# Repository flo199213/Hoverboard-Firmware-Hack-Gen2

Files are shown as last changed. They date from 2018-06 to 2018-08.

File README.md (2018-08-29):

#### Updates:
````
- Firmware is ready.
- Sadly I can not support any issues. I'm not a student, less free time :)
````

### Hoverboard-Firmware-Hack-Gen2

Hoverboard Hack Firmware Generation 2 for the Hoverboard with the two Mainboards instead of the Sensorboards (See Pictures).

This repo contains open source firmware for generic Hoverboards with two mainboards. It allows you to control the hardware of the new version of hoverboards (like the Mainboard, Motors and Battery) with an arduino or some other steering device for projects like driving armchairs.

The structure of the firmware is based on the firmware hack of Niklas Fauth (https://github.com/NiklasFauth/hoverboard-firmware-hack/). Because of a different model of processor (GD32F130C8 instead of STM32F103) it was not possible to use the same firmware and it has to be written from scratch (Different hardware, different, pins, different registers :( )

- This project requires knowledge of the initial project linked above.
- At the current point I am not able to support any questions or issues - sorry!

---

#### Hardware
otter

The hardware has two main boards, which are different equipped. They are connected via USART. Additionally there are some LED PCB connected at X1 and X2 which signalize the battery state and the error state. There is an programming connector for ST-Link/V2 and they break out GND, USART/I2C, 5V on a second pinhead.

The reverse-engineered schematics of the mainboards can be found here:
https://github.com/flo199213/Hoverboard-Firmware-Hack-Gen2/blob/master/Schematics/HoverBoard_CoolAndFun.pdf

---

#### Flashing
The firmware is built with Keil (free up to 32KByte). To build the firmware, open the Keil project file which is includes in repository. Right to the STM32, there is a debugging header with GND, 3V3, SWDIO and SWCLK. Connect GND, SWDIO and SWCLK to your SWD programmer, like the ST-Link found on many STM devboards.

- If you never flashed your mainboard before, the controller is locked. To unlock the flash, use STM32 ST-LINK Utility or openOCD.
- To flash the STM32, use the STM32 ST-LINK Utility as well, ST-Flash utility or Keil by itself.
- Hold the powerbutton while flashing the firmware, as the controller releases the power latch and switches itself off during flashing

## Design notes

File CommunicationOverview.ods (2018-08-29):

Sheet: Frames
Direction | Byte Count | 0 | 1 | 2 | 3 | 4 | 5 | 6 | 7 | 8 | 9 | 10
Master → Steering | 2 | / | \n
 |  | char | char
Steering → Master | 8 | / | Speed |  | Steer |  | CRC |  | \n
 |  | char | int16 |  | int16 |  | uint16 |  | char
Master → Slave | 10 | / | PWM |  | Identifier | Value | value | Bits | CRC |  | \n
 |  | char | int16 |  | uint8 | int16 |  | uint8 | uint16 |  | char
Slave → Master | 5 | / | Bits | CRC |  | \n
 |  | char | uint8 | uint16 |  | char
Slave → Bluetooth | 11 | / | Identifier |  | 0 | ± | Value |  |  |  |  | \n
 |  | char | char1 | char2 | uint8 | char | char1 | char2 | char3 | char4 | char5 | char
Bluetooth → Slave | 11 | / | Identifier |  | Read/Write | ± | Value |  |  |  |  | \n
 |  | char | char1 | char2 | uint8 | char | char1 | char2 | char3 | char4 | char5 | char

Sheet: Identifierlist
Slave ↔ Bluetooth
Identifier | Meaning | Location | Range
0 | Battery Master | Master | Value*100
1 | Current DC Master | Master | Value*100
2 | Current DC Slave | Slave | Value*100
3 | Real Speed Master | Master | Value*100
4 | Real Speed Slave | Slave | Value*100
5 | Beeps backwards | Master | Off=0, On=1
6 | Music Box (Master lower) | Master | Off=0, On=1
7 | Horn (Master upper) | Master | Off=0, On=1
8 | LED Hue | Slave | 0-764
9 | LED Saturation | Slave | 0-128
10 | LED Brightness | Slave | 0-63
11 | LED Mode | Slave | LED_OFF = 0, LED_HSB = 1, LED_HSB_BLINK = 2, LED_HSB_FADE = 3, LED_HSB_STROBE = 4
12 | LED Fading Speed | Slave | 200-1000
13 | LED Blink Speed | Slave | 700-2400
14 | LED Strobe Speed | Slave | 0-1000

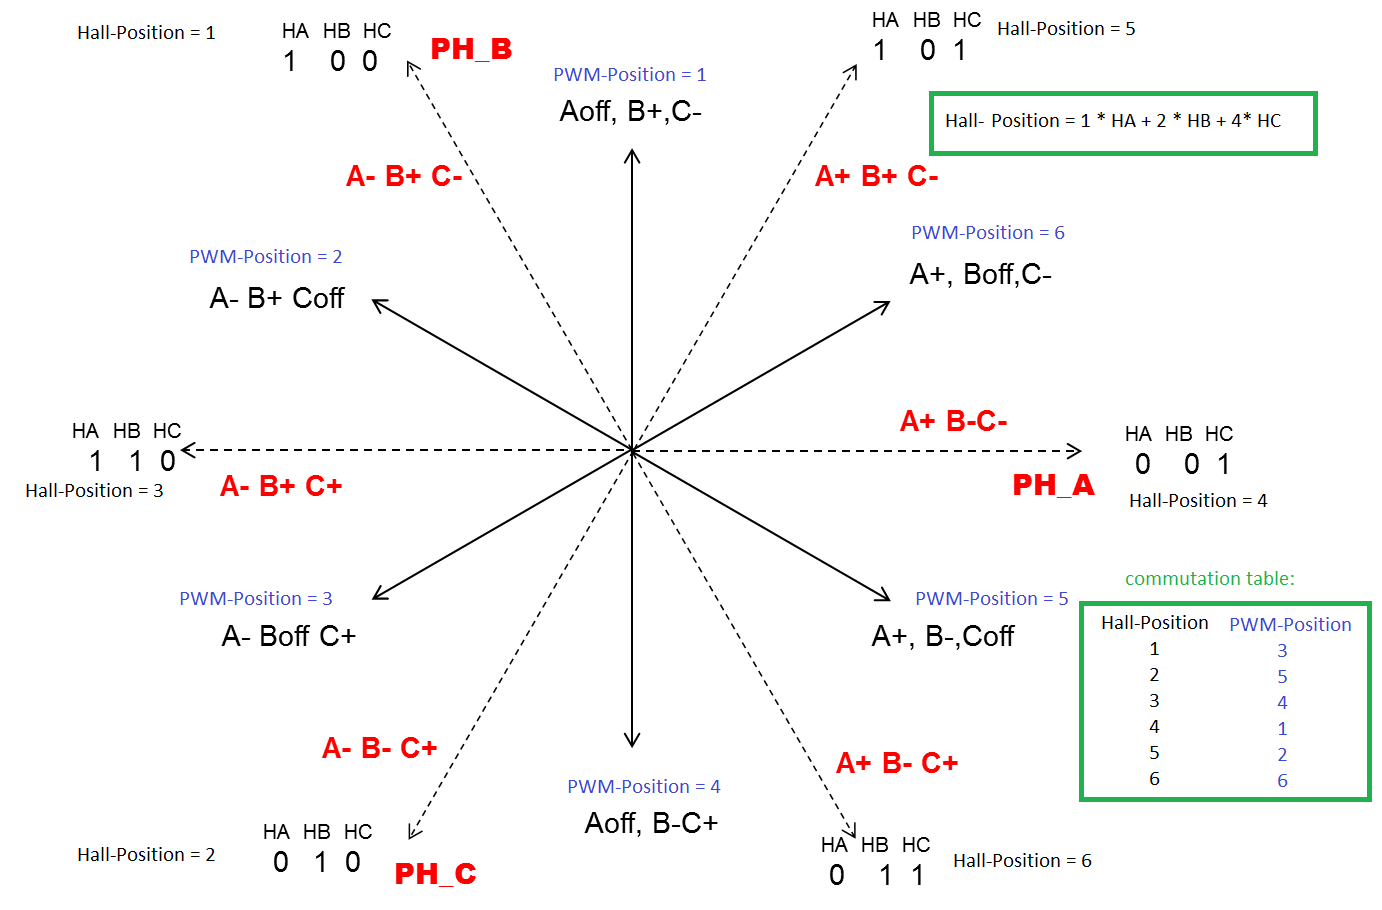
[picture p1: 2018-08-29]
Raumzeigerdiagramm.png

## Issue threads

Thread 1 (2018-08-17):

Updates

drbytes, 2018-08-17:
I've managed to flash the two boards from a eslide 650 with this.
Had to unlock the firmware first on both boards and solder a header. My boards have a different layout. This is the first time working with STLINK/STM32, 0 prior experience but flashing with the keil sdk went well, just keep holding the power button or it doesn't work. Good job on this firmware, I'll see if I can get it to interface with a pi this weekend.
Is the work on this ongoing?

gaucho1978, 2019-04-13:
I'll try the same. Is it a way to restore the hoverboard after playing with this hack?

Closed 2018-08-17.

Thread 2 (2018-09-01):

#include "arm_math.h"

drbytes, 2018-09-01:
Hi, I installed all the relevant software packs in Keil uVision ... at least that what I thought but I get a compilation error in main.c around line
`47: #include "arm_math.h" `
resulting in
```
Src\main.c(47): error:  #5: cannot open source input file "arm_math.h": No such file or directory
  #include "arm_math.h"
```

Do you know what I'm missing? (keil n00b)

drbytes, 2018-09-01:
I've commented the line and it builds.

Johnvan, 2019-02-24:
I have a similar problem with an adafruit MP3 program that uses arm_math.h, what do I have to do to fix this thing.
ERROR: arm_math.h: No such file or directory

pieterjanbuntinx, 2019-02-26:
It now works for me. To solve the other error I got I had to enable this:
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

Johnvan, 2019-02-28:
I have no idea what you are trying to tell me about **Enabling this,** what and how. Where is this Options for Target.

gaucho1978, 2019-04-19:
> You have to include the path C:\Keil_v5\ARM\PACK\ARM\CMSIS\5.4.0\CMSIS\Include in the "Options for Target..."  > C/C++. Afterwards it compiles al the c-files but it gets stuck on the other issue that's reported in this repo.

in my case the correct folder is: C:\Users\GauchoHP\AppData\Local\Arm\Packs\ARM\CMSIS\5.5.1\CMSIS\Include

after doing this it correctly compile.

renmalek7, 2020-04-08:
Hi. Were you able to flash this firmware?

Johnvan, 2020-04-09:
I updated my IDE and the fault went away. Thankyou for your assistance however, much appreciated.

weiminshen99, 2023-05-19:
The <arm_math.h> and other related .h files may also be found at this repository:
https://github.com/PaulStoffregen/arm_math

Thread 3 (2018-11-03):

Hoverboard.axf not found

bugiworks, 2018-11-03:
I appreciate your work, after 1 board hoverboard, i want to try this one also.

when i try to build with keil, i get the error
.\Objects\Hoverboard.axf: error: L6031U: Could not open scatter description file .\Objects\Hoverboard.sct: No such file or directory
Not enough information to list image symbols.
Not enough information to list load addresses in the image map.
Finished: 2 information, 0 warning, 0 error and 1 fatal error messages.
".\Objects\Hoverboard.axf" - 1 Error(s), 0 Warning(s).
Target not created.

any solution? or any direct hex files do you have?
By the way, the board im using has GD32F103 not F130, i have downloaded the pack for 103 but im not sure if it works same.

pieterjanbuntinx, 2018-12-21:
Hi @kevin0932,
No, I did not. But I found [a fork](https://github.com/btsimonh/Hoverboard-Firmware-Hack-Gen2) of this repo that compiles. I have not managed to get it uploaded to my hoverboard controller, I don't have a STLink but I'm using a STM32 Discovery board, so that's probably the problem.

bugiworks, 2018-12-25:
Unfortunately i couldnt find any solution.

pieterjanbuntinx, 2019-02-26:
It now works for me. To solve this error I had to enable this:
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

renmalek7, 2020-04-08:
Hi. Were you able to flash this firmware?

pieterjanbuntinx, 2020-04-08:
Yes, I was able to flash it. It works great. What are you stuck on?

renmalek7, 2020-04-08:
I have a different board, it's also a GD32F130. Before flashing the firmware, How can I tell if the Pins are the same?
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

pieterjanbuntinx, 2020-04-08:
You could perhaps measure continuity using a multimeter from the pins of the MCU to the peripherals. If that corresponds to the pinout in the code it should work. That will be quite some work though, so if you think that the layout of the PCB looks about the same as the one of this repo, you could perhaps just try it out (at your own risk). Replacement boards are not that expensive from AliExpress

renmalek7, 2020-04-08:
ok, I will do that and post the results. Do you know if there is a way to pull the original firmware from the board? Would it be posible to write it back in the board if I fail and its not burned l?

pieterjanbuntinx, 2020-04-08:
No I don't think so. I thought it was locked or something. It has something to do with the options bytes

renmalek7, 2020-04-08:
ok, thank you very much for you time : )

Harsh2210, 2020-06-16:
> I have a different board, it's also a GD32F130. Before flashing the firmware, How can I tell if the Pins are the same?
> 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

Were you able to flash the firmware? I am using the same motherboard. I wanted to know whether the pinouts are same for this one.

yodaco, 2022-07-23:
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

Did it work?!?

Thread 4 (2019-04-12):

Use Pwm or ppm input, avoiding the need of arduino

gaucho1978, 2019-04-12:
Can I modify your code to control hoverboard via ppm or 3 pwm instead of a uart?
Can I use the following inputs to receive pwm or ppm?:
-pa7(L1)
-pa11(L2)
-pc15(switch k1)

Can I use external switch instead of K1 switch in order to assign to it another funcion?

Can I use pc13(x3.1 output) or pa1(x2.1 output) to generate a pwm signal?

gaucho1978, 2019-05-12:
done here: https://github.com/gaucho1978/CHEAP-LAWNMOWER-ROBOT-FROM-HOVERBOARD/blob/master/README.md

Closed 2019-05-12.

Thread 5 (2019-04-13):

Restore hoverboard

gaucho1978, 2019-04-13:
Is it there a way to restore the hoverboard after playing with this hack?

teixeluis, 2019-06-21:
That is a pertinent question. Anyone have been successful at dumping the original firmware via ST-Link? Is it locked in most of not every board?

If a dump of the firmware + eeprom + config bits is feasible, eventually the device could be restored (I would put very little hope that the device flash is not protected though..).

Cheers,

Luis Teixeira

renmalek7, 2020-04-06:
Anyone did it?

renmalek7, 2020-04-08:
Hi. Were you able to flash this firmware?

weiminshen99, 2023-05-19:
I have saved the original flash for both Master and Slave board, if anyone is still interested.

teixeluis, 2023-05-19:
@weiminshen99  cool. Yes I would have interest in taking a peek. Cheers

weiminshen99, 2023-05-19:
The saved .bin files are at https://github.com/weiminshen99/GD32-hover-master-slave.git, under the directory Factory_Flash.

I have saved them after I unlocked boards, but I never test them because my boards are all occupied for other purposes. Good luck, and let me know if they work or not. Thanks!

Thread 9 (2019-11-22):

Mention "TT-SD2.2" in docs

gnbl, 2019-11-22:
It should be mentioned that this project is based on a PCB with silkscreen markings "TT-SD2.2", which seems to be a TaoTao hoverboard controller.
I have two of these, one 6.5" Cool&Fun and an 8" "M110".
The former has water damage on the primary control board and fries the high-side switch of phase A. It seems I'll have to dig through the conformal coating to measure whether the drivers or the sensing or even the MCU is defective...

renmalek7, 2020-04-08:
Hi. Were you able to dig through the coating? Were you able to flash the firmware?

gnbl, 2020-04-24:
I have not yet attempted reflashing nor repair.

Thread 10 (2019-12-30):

Please add a makefile for my online compiler :-)

RoboDurden, 2019-12-30:
Hello from Germany :-)
I would like to add your repo to my online compiler www.pionierland.de/hoverhack
videos: https://www.youtube.com/playlist?list=PLa9VLvJBLbTMmpslED2FMClIBv5URBMIa

But you only offer the Keil project files. If you are already compiling with GCC, a port should be possible: https://community.arm.com/developer/tools-software/oss-platforms/f/gnu-toolchain-forum/45142/how-to-move-from-keil-to-linux

Ideas welcome !
www.robo4future.de :-)

RoboDurden, 2020-01-14:
no answer :'(

renmalek7, 2020-04-06:
Hello. Were you able to move the repo to your online compiler? I am working with this firmware and I would appreciate your advice. Could you please mail me to renmalek7@gmail.com

Thank you very much : )

RoboDurden, 2020-04-06:
No, i am not experienced enough to copy and paste a Makefile :-/
A pity because adding repos to my online compiler just takes one line of code. Today i added all three repos of  https://github.com/EmanuelFeru

renmalek7, 2020-04-06:
What about Florian's firmware (this branch)? Were you able to flash it in a Gen2 board?

RoboDurden, 2020-04-06:
I have no Gen2 board where there is a control board for either side.

renmalek7, 2020-04-06:
Do you have 20 min for a video call? I am having trouble with the firmware and maybe you can advise me. Do you have skype?

renmalek7, 2020-04-08:
please, I just need someone to tell me how to indentify the pin conection in the board : (

RoboDurden, 2020-04-08:
You are spoliing my issue here to kindly ask for a makefile.

renmalek7, 2020-04-08:
I am really sorry. Thats why I left my email. Could you plase help me?

bricobi5, 2022-06-05:
Hi I have 4 gen2 motherboard that I can't flash so I try Florian's firmware
but where can i find it?

RoboDurden, 2022-06-05:
https://github.com/flo199213/Hoverboard-Firmware-Hack-Gen2/tree/master/HoverBoardGigaDevice
But as it still has no makefile, i can not include it to my online compiler :-(
I guess you have to install Keil to open the .uvoptx µVision 5 project files :-((
Someone who does not dislike Linux so strongly as i do might easily generate that makefile for me/us :-/

BastelPichi, 2022-07-23:
> https://github.com/flo199213/Hoverboard-Firmware-Hack-Gen2/tree/master/HoverBoardGigaDevice But as it still have no makefile, i can not include it to my online compiler :-( I guess you have to install Keil to open the .uvoptx µVision 5 project files :-(( Someone who does not dislike Linux so strongly as i do might easily generate that makefile for me/us :-/

Incoperating #16 may fix the issue. Compiling with PIO should be possible, but i dont know what amount of recoding this would take.

RoboDurden, 2022-07-23:
For a Linux believer a make file should be no issue at all. But I am rather a Linux hater.
Yet if you tell me how to install PlatformIO on my Ubuntu vserer and which exact command line will successfully compile the firmware, I would add platform Io support to my online compiler :-)

BastelPichi, 2022-07-24:
Well to install PIO, you get quite good docs here: [https://docs.platformio.org/en/latest/core/installation/methods/index.html](https://docs.platformio.org/en/latest/core/installation/methods/index.html)

To compile the project, all you need to do is run `pio run` in the `HoverBoardGigaDevice`directory.
The build is saved at `HoverBoardGigaDevice/.pio/build/GD32F130C8T6/` theres a firmware.bin and a firmware.elf, I assume they are both the same, but I would try to firmware.elf first.

The first build takes quite some time as it downloads alot, however then builds run within a few seconds.

PS: Lol ich könnte auch einfach Deutsch schreiben
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

BastelPichi, 2022-09-03:
Any update on this?

RoboDurden, 2022-09-03:
no time (time = happiness) to add the PIO support. sorry.

BastelPichi, 2022-09-04:
Ok, I broke my STLink anyways for now xD

weiminshen99, 2023-04-24:
Here is a repository for Makefile, if you are still interested:
https://github.com/weiminshen99/GD32-hover-master-slave

RoboDurden, 2023-04-24:
Yes great,  i still would like to add a gen2 firmware to my online compiler.
Your folder structure

https://github.com/weiminshen99/GD32-hover-master-slave/tree/main/Drivers/GD32F1x0_standard_peripheral/Source

 is a bit different then my gen 2.x firmware

https://github.com/RoboDurden/Hoverboard-Firmware-Hack-Gen2.x/tree/main/HoverBoardGigaDevice/RTE/Device/GD32F130C6

But I guess I can port your makefile.

If your makefile generates a working gen2.0 binary i would add your report to my online compiler. It might take a year before I proceed with the makefile for my repo...

RoboDurden, 2023-04-24:
no but i have made quite a lot of reverse engeniering: https://github.com/RoboDurden/Hoverboard-Firmware-Hack-Gen2.x/tree/main/Schematics_2.0

RoboDurden, 2023-04-26:
So i have added your repo to my online compiler. But i forked it because i needed to switch to a gcc inline compiler directive. Still get a warning

```
Src/bldc.c:90:38: warning: always_inline function might not be inlinable [-Wattributes]
   90 | __attribute__((always_inline))  void blockPWM(int pwm, int pwmPos, int *y, int *b, int *g) //org __INLINE not known in gcc

```
but the code compiles:  https://pionierland.de/hoverhack/?p=gen2
Maybe someon can test it.

I also needed to increase a char buffer from 5 to 7 in comsBluetooth.c to remove sprintf warnings:

```
void SendBluetoothDevice(uint8_t identifier, int16_t value)
{
	int index = 0;
	char charVal[7];

```

This should also apply to your compiler ?

Thanks again.

weiminshen99, 2023-04-26:
Thanks for adding my repo!

I have made the two changes you suggested and compiled here successfully and pushed the changes into my repo.

If you like, you could try to compile again to see if you can get rid of the warming (replace “_INLINE” by “inline”).

Have a good day!

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

RoboDurden, 2023-04-27:
Yes i would like to add your original and not my fork so you might be motivated to get involved.
But I had already tried the official c inline and it does.not compile:

/usr/lib/gcc/arm-none-eabi/9.2.1/../../../arm-none-eabi/bin/ld: build/bldc.o: in function `CalculateBLDC':
/var/www/html/pionierland/public/hoverhack/source/robodurden_gd32-hover-master-slave/Src/bldc.c:214: undefined reference to `blockPWM'
collect2: error: ld returned 1 exit status
make: *** [Makefile:185: build/firmware.elf] Error 1

I can remove the inline altogether and i compiles without warning. Is that function really that time critical that there is no time to make a function call ?

RoboDurden, 2023-04-27:
I See that the blockPWM function is used only once anyway : https://github.com/weiminshen99/GD32-hover-master-slave/blob/main/Src/bldc.c#L214

So simply copy the code there ?

I think it should be possible to make the function code a #define , that might be another was to get rid of that inline word ?

weiminshen99, 2023-04-27:
I have taken out the “__INLINE”, and please compile again. Thanks!

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

RoboDurden, 2023-04-27:
Fine, i switched the repo back to yours :-)

https://pionierland.de/hoverhack/?p=gen2

Would be nice if you could add a simple arduino example that spins the two motors a bit forward and backwards.
This seems to be too much: https://github.com/gaucho1978/CHEAP-LAWNMOWER-ROBOT-FROM-HOVERBOARD/tree/master/ArduinoFirmware

For my Gen 2.x firmware i rewrote all the serial communication, so people can not rely on my arduino example when using your firmware.
The original https://github.com/flo199213/Hoverboard-Firmware-Hack-Gen2/tree/master/PPMDeviceArduino_V1.0/PPMDevice is also overloaded with PPM rc-control :-/

Ideas welcome :-)

weiminshen99, 2023-04-28:
Please open an issue at the repos: https://github.com/weiminshen99/GD32-hover-master-slave
and I will add something as you requested there. Thanks!

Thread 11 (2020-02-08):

GD32F103 board?

abrarakram19, 2020-02-08:
Can this firmware be flashed on two red coloured boards with GD32F103 MCU? Please let me know if it is possible or any link for this type.

renmalek7, 2020-04-08:
Hi. Were you able to flash this firmware in those red boards? Do you still need help?

baranchuk, 2020-04-10:
I try to flash it on red boards. It not work for me

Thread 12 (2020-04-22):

Error flashing with ST-LINK utility

JMarceloCasanova, 2020-04-22:
Hello! I'm having an error flashing the firmware with ST-LINK.

So what I have done is: compiled the firmware with Keil to have the binaries, connected the st-link v2 with the board and unlocked the flash by resetting the option bytes, cleared the memory and then I get this error:
: Unexpected error
: Error occured during program operation!
: Programming error @ 0x08000000!
I'v tried pressing the button and changing some speeds but with no success.

My board's model is TT-SD2.2 with a gd32f130c8t6

andresiko, 2020-07-22:
Any progresa @JMarceloCasanova ?

drphil3d, 2022-02-02:
having the same issue

rokars, 2022-06-06:
i used the keil flash -> download to program directly from keil, works

AlfreddGco, 2023-12-01:
Try with `st-flash --reset write ./firmware.bin 0x08000000`

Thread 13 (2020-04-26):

Split Board "Jiaan" with GD32F130C6

t-oster, 2020-04-26:
Hi,

I have a Hoverboard with two almost identical boards labeled "Jiaan". I am trying to get this to work, however I am not experienced with ARMs so far (only AVRs) and not so used to reverse engineering.
I already found out it uses a GD32F130C6 instead of GD32F130C8 (32kb instead of 64kb flash etc).
I unlocked both controllers and I can flash files, which can successfully be read after that, so I think flashing is fine.
I guess the basics are similar to the boards this firmware is written for, but there must be differences (e.g. other PINs used?). I'd like to provide a patch for this firmware to also work with those boards, but I'm stuck.

I am trying to get some answer from the board, I tried to send something on both USARTs or blink some Pin I think is connected to an LED but nothing so far.

Has anybody already seen this board an can help me out?

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

t-oster, 2020-04-29:
At least the Master/Slave UART seems to be on the correct PINs. I can communicate with the controller now. Any Idea how I can find out the pin-assignments without destructing the board? It's not easy for me to follow the tracks on the board, but I guess I should not just set all pins as output and set/reset them in order to look for which LED is blinking or if the motor does something, because if there is an output from another IC connected I might short circuit it...

t-oster, 2020-04-30:
OK, now I know the Pins for the Light-Barriers, the Buzzer, the hall sensor, power button and power-latch.
Now I only need to find the pins for the 6 channels for the motor. Any idea how I can easily trace them? I guess if I accidentally switch the same channel high and low at the same time I would get a short circuit? Are the outputs usually pulled up or down externally?

t-oster, 2020-05-02:
Nevermind, I got it to work basically. The motors are on the same pin as on your board. The biggest problem with mine is that the second UART is not broken out, so I have to use the TX for the slave and the RX for the arduino....
maybe I will send a PR after cleaning a bit. However here are my PINs so far:
```c
#ifndef DEFINES_H
#define DEFINES_H

#include "gd32f1x0.h"
#include "../Inc/config.h"

// LED defines

#define UPPER_LED_PIN GPIO_PIN_5
#define UPPER_LED_PORT GPIOB
#define LOWER_LED_PIN GPIO_PIN_8
#define LOWER_LED_PORT GPIOB

// Brushless Control DC (BLDC) defines
// Channel G
#define RCU_TIMER_BLDC RCU_TIMER0
#define TIMER_BLDC TIMER0
#define TIMER_BLDC_CHANNEL_G TIMER_CH_2
#define TIMER_BLDC_GH_PIN GPIO_PIN_10
#define TIMER_BLDC_GH_PORT GPIOA
#define TIMER_BLDC_GL_PIN GPIO_PIN_15
#define TIMER_BLDC_GL_PORT GPIOB
// Channel B
#define TIMER_BLDC_CHANNEL_B TIMER_CH_1
#define TIMER_BLDC_BH_PIN GPIO_PIN_9
#define TIMER_BLDC_BH_PORT GPIOA
#define TIMER_BLDC_BL_PIN GPIO_PIN_14
#define TIMER_BLDC_BL_PORT GPIOB
// Channel Y
#define TIMER_BLDC_CHANNEL_Y TIMER_CH_0
#define TIMER_BLDC_YH_PIN GPIO_PIN_8
#define TIMER_BLDC_YH_PORT GPIOA
#define TIMER_BLDC_YL_PIN GPIO_PIN_13
#define TIMER_BLDC_YL_PORT GPIOB

// Timer BLDC short circuit emergency shutoff define
#define TIMER_BLDC_EMERGENCY_SHUTDOWN_PIN GPIO_PIN_12
#define TIMER_BLDC_EMERGENCY_SHUTDOWN_PORT GPIOB

// Hall sensor defines
#define HALL_A_PIN GPIO_PIN_0
#define HALL_A_PORT GPIOA
#define HALL_C_PIN GPIO_PIN_11
#define HALL_C_PORT GPIOB
#define HALL_B_PIN GPIO_PIN_1
#define HALL_B_PORT GPIOA

// Usart master slave defines
#define USART_MASTERSLAVE USART1
#define USART_MASTERSLAVE_TX_PIN GPIO_PIN_2
#define USART_MASTERSLAVE_TX_PORT GPIOA
#define USART_MASTERSLAVE_RX_PIN GPIO_PIN_3
#define USART_MASTERSLAVE_RX_PORT GPIOA

// ADC defines
#define VBATT_PIN	GPIO_PIN_4
#define VBATT_PORT GPIOA
#define VBATT_CHANNEL ADC_CHANNEL_4
#define CURRENT_DC_PIN	GPIO_PIN_6
#define CURRENT_DC_PORT GPIOA
#define CURRENT_DC_CHANNEL ADC_CHANNEL_6

// Self hold defines
#define SELF_HOLD_PIN GPIO_PIN_2
#define SELF_HOLD_PORT GPIOB

// Button defines
#define BUTTON_PIN GPIO_PIN_5
#define BUTTON_PORT GPIOA

// Buzzer defins
#define BUZZER_PIN GPIO_PIN_9
#define BUZZER_PORT GPIOB

// Charge state defines
#define CHARGE_STATE_PIN GPIO_PIN_15
#define CHARGE_STATE_PORT GPIOC

Closed 2020-05-02.

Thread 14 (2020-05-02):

ADC control with two potentiometers

vischio96, 2020-05-02:
Hi all,

these two identical mainboards are pretty common in hoverboards, and i have a lot of them at home. Does anyone know if there's a way to control the two boards with 2 differents ADC inputs (ex two potentiometers) as the mainboard that NiklasFauth uses?

From the reverse engineered schematics i see that the two lightbarriers sensors uses two ADC pins (PA7 and PA11) and they seems unused in the code, but i'm not that good at programming.
The only way i know to control these mainboards is using PPM with an Arduino board.

Could anyone help me? Thank you a lot.

andresiko, 2020-07-22:
Have you succeeded flashing these boards? I have an tt-sd 2.2 with gd32f130c8t6, and I don't know if this firmware will work on it.

zulkep, 2021-06-16:
have you got to connect the potentiometers directly to the board?

Jebumon, 2022-04-25:
Hi all,

I have hoverboard control board, using GD32F130C8T6. Anyone know how to re-program his MCU ?
could anyone help me ?

alexei0kazachina, 2023-06-02:
Да пишите мне, я смогу помоч.

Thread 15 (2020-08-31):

No compiling , error in adc

centiane, 2020-08-31:
No compiling ok, this error show, help me, please.

*** Using Compiler 'V5.06 update 6 (build 750)', folder: 'C:\Keil_v5\ARM\ARMCC\Bin'
Rebuild target 'Target 1'
compiling setup.c...
Src\setup.c(343): error:  #167: argument of type "dma_parameter_struct" is incompatible with parameter of type "dma_parameter_struct *"
  	dma_init(DMA_CH0, dma_init_struct_adc);
Src\setup.c(365): error:  #20: identifier "ADC_EXTTRIG_REGULAR_SWRCST" is undefined
  	adc_external_trigger_source_config(ADC_REGULAR_CHANNEL, ADC_EXTTRIG_REGULAR_SWRCST);
Src\setup.c(424): error:  #167: argument of type "dma_parameter_struct" is incompatible with parameter of type "dma_parameter_struct *"
  	dma_init(DMA_CH4, dma_init_struct_usart);
Src\setup.c(480): error:  #167: argument of type "dma_parameter_struct" is incompatible with parameter of type "dma_parameter_struct *"
  	dma_init(DMA_CH2, dma_init_struct_usart);
Src\setup.c: 0 warnings, 4 errors

cfox570, 2020-10-18:
It looks like the uVision IDE has new libraries that are required.  I am rebuilding the project with uVision and will add the source to it.  I will update my comment when I have additional results.

mmaslyukov, 2021-01-25:
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

Recently tried to compile it, but got the same errors. However after downgrading GigaDevice pack to 3.1.0 and going through steps mentioned in other threads I was able to successfully build it.
Here is a brief list of neccessery steps to do

1. Use  GigaDevice.GD32F1x0_DFP.3.1.0.pack, version 3.2.0 will not do
2. In uVision project settings (C/C++ tab) add "C:\Users\<your_user_name>\AppData\Local\Arm\Packs\ARM\CMSIS\5.7.0\CMSIS\Include" to include path
3. In uVision project settings (Linker tab)  set checkbox: "Use Memory Layout form Target Dialog". It is necessary for generation of  Hoverboard.sct file
4.  Compile

Dennis-Gee, 2021-06-08:
Hello, the GigaDevice.GD32F1x0_DFP.3.1.0.pack is no longer available. could someone compile the two firmwares and upload ist somewhere so the project isnt dying?

cfox570, 2021-06-08:
You need to get GD32F1x0_Addon_V3.1.0.rar from  http://www.gd32mcu.com/en/download/7/p/2   Use the pack installer to downgrade to 3.1.

rokars, 2022-06-06:
3.1.0 pack available here https://github.com/gearsincorg/Hoverboard_Utility_Gateway_System

alexismailov2, 2024-08-11:
using 3.1.0 fixed previous problems but. Apeared additional problem
.\Objects\Hoverboard.axf: error: L6031U: Could not open scatter description file .\Objects\Hoverboard.sct: No such file or directory
Could someone help?

IrokezPetrovic, 2025-06-02:
In SPL 3.10:
`#define ADC_EXTTRIG_REGULAR_SWRCST      CTL1_ETSRC(7)                       /*!< software trigger select for regular channel */`
In newer versions of SPL:
`#define ADC_EXTTRIG_REGULAR_NONE        CTL1_ETSRC(7)                       /*!< software trigger */`

To use SPL newer than 3.1.0 - replace `ADC_EXTTRIG_REGULAR_SWRCST` to `ADC_EXTTRIG_REGULAR_NONE`

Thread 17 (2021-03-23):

How to flash?

casperround, 2021-03-23:
When flashing do you have to flash both boards? I've flashed the main master successful, powered on and the slave board operates like stock. So wondering if I need to flash that side too??

FGay, 2021-05-01:
you need to flash both sides but you have to rebuild the code with a change in the config.h file
for the master board you can leave everything as is but for the slave board you need to change "#define MASTER" to "//#define MASTER" and also you have to uncomment the "#define SLAVE"

szepnorbee, 2021-05-08:
> you need to flash both sides but you have to rebuild the code with a change in the config.h file
> for the master board you can leave everything as is but for the slave board you need to change "#define MASTER" to "//#define MASTER" and also you have to uncomment the "#define SLAVE"

Hi FGay! Have you tried this firmware? I tried Pro Mini and ESP8266, but no response. I try to access it on MASTER using the example code.(PPMDevice) The controller sends the data, the arduino sends the response, but nothing. The board is good because I can start the motors at a fixed speed by modifying the code (board firmware). Can you help me?  Thank you.

FGay, 2021-05-09:
@szepnorbee
i also have issues.
The board sends the data properly. My arduino nano/uno is not capable of listening to the board on its RX pin. (dont know why though)
I tried using software serial and now the communication between the arduino and the hoverboard works.
But the motors are not moving. I also tried to spin the motors at a constant speed by modifying the board firmware but i was not able to get it to work. (the hoverboard was perfectly fine before the flash so i dont think that its an hardware issue)
I also used the example code but modified it slightly so i can adjust the speedvalue with a potentiometer.
I think we might have a similar problem here.
How does your modified board firmware look like?

szepnorbee, 2021-05-09:
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

Yes, I have solved the problem. There were two things. The first was that my board had a bluetooth interface which is not shown in the photo. I soldered it down because it was occupying the USART ports. The second problem is that the arduino code called PPMDevice is broken. It originally sends 9 bytes instead of 8. The one line in SteeringSerial.cpp needs to be commented out. This: // buffer[index++] = sendByte;

After doing this, everything works immediately.

I use this fork now because it has PID and you can control the two motors separately: https://github.com/pieterjanbuntinx/Hoverboard-Firmware-Hack-Gen2

Good luck, I hope I helped.

Translated with www.DeepL.com/Translator (free version)

FGay, 2021-05-10:
I am so happy. IT WORKS NOW!!
Thank you very much!

rohitsahu7, 2021-07-31:
Hello Great to hear ..congrats for your project . I need help regarding the project compiling in Keil , I am getting errors, i have  not modified anything still getting errors basically in timers,
Please help , i have attached picture
thank you

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

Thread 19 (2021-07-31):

Compiling error in Keil project

rohitsahu7, 2021-07-31:
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

Please help debug errors ,I have opened the project in Keil and it is giving compiling errors

Do i need to use any specific version of Keil?

attached Image of list of errors
basically errors are related to timers

FGay, 2021-08-07:
Have you tried the steps mentioned here? [#15 No compiling , error in adc](https://github.com/flo199213/Hoverboard-Firmware-Hack-Gen2/issues/15#issuecomment-766647385)

crazyone151, 2022-10-29:
the link is dead

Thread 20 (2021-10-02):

What accelerometer/gyroscope chip does the board actually have?

qwandor, 2021-10-02:
The schematic here says that there's an MPU6050 connected to I2C2 on PB8/PB9, but this seems not to be accurate. For a start PB8/PB9 is I2C0 not I2C2, but more importantly there doesn't seem to be any MPU6050 on the board.

There are however two chips that I haven't been able to identify: U2 and U5. I'm struggling to read the markings on them, but U2 is marked something like "ATG BS." while U5 is marked "TP09. 1828 H1" or something similar. Has anyone been able to figure out what these chips are, and whether one of them is the sensors?

qwandor, 2021-10-02:
To confuse matters, looking at another board, the chips are different: on this one U2 is "BOP BS." and U5 is "TP09. 1822 H1".

Candas1, 2021-11-05:
Hi,

It could be there are different versions of the board with different IMUs also.

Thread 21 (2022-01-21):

ARM MM32SPIN06 YS-SXT-4.2 - HOVER-1 Board

landgrant, 2022-01-21:
I recently purchased a HOVER-1 CHROME hoverboard. Inside it had the split boards similar to the main post but has a different processor I have not seen. I cannot get the board to connect on ST-LINK, and not sure if the pinout is the same as others have seen with their split boards. The main board is labeled YS-SXT-4.2 A, the slave is YS-SXT-4.2 B. I installed the MDK ARM tool from KEIL, but STM32Cube and ST-LINK still have no luck connecting.

https://imgur.com/a/8aWoPEG

I haven't seen anything online with info, but wanted to see if anyone had any tips.

robinsingh1, 2022-04-25:
Were you able to find an answer here ?

landgrant, 2022-04-25:
Unfortunately not. I ended up buying single boards off of eBay for one
project, and separate brushless controllers for another

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

--

*ADAM BENNER**PRESIDENT*
614 / 398-1622
***@***.***

WEB <http://landgrantbrewing.com/>   /   FACEBOOK
<http://www.facebook.com/landgrantbrewingco>   /   TWITTER
<https://twitter.com/landgrantbeer>

Kambodia91, 2023-04-11:
look: https://github.com/Kambodia91/Hoverboard-firmware-hack-FOC-MASTER-SLAVE

Alshawa994, 2024-09-05:
I'm working on the same Motherboards, and this can help you. It is also helpful to know which Processor you have on it. mine was MM32SPIN05PF on a YS-SXT-V4.2 A & B.

here is the link
https://github.com/AILIFE4798/Hoverboard-Firmware-Hack-Gen2.x-MM32/blob/main/README.md

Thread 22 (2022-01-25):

Anything bldc motor?

nazariiixa, 2022-01-25:
Hello, nice project, I test it and all works! I want to change u code for working with any bldc motor (with or without halls sensors, and with another numbers of magnets)... How its possible to do?

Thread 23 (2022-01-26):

Pin-out for ADC (potentiometer)

Kipyeah, 2022-01-26:
Hi al almost complete n00b here. Did anyone find and had succes with controlling these Splitboards with ADC (potentiometers). Im try to build a hovercart type thing.

jeromebg, 2022-02-17:
Hello, trying to do the same, did you found a solution ?

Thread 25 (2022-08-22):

no movement

Windaube, 2022-08-22:
hello
I managed to compile and flash the two cards with the master and slave versions.

I also program the arduino with the code provided.

the master card sends many frames to the arduino but the arduino does not respond and therefore the hoverboard does not start.

Do you have an idea of   the problem ?

RoboDurden, 2023-02-01:
You can now download compiled binaries for the V2.0 and V2.1 boards as well as tested Arduino examples on my fork: https://github.com/RoboDurden/Hoverboard-Firmware-Hack-Gen2.x

I can only test the PPM rc-receiver Arduino example with OVERWRITE_PPM as i do not have an rc-controller. Please share feedback.

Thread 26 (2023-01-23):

RC Receiver

WolfgangDerVollstrecker, 2023-01-23:
any way to control the split board with PWM from an RC Receiver?

RoboDurden, 2023-01-30:
I guess we neeed to help ourselves..
this firmware seems to only support uart control. So better add a $3 ESP32 S2 Mini to your project which will add bluetooth and wifi, etc.

Of course you could add code to read a pwm signal from the RX pin.
Speed and steer are set in https://github.com/flo199213/Hoverboard-Firmware-Hack-Gen2/blob/e138b221aed944478d12e15d81fb858f44f4a289/HoverBoardGigaDevice/Src/commsSteering.c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

And here you can find the code to implement pwm: https://github.com/EFeru/hoverboard-firmware-hack-FOC/blob/efb438bf514c9f8c80471f79ab87d2f7099746ea/Src/control.c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

But i strongly suggest you add the esp32..

ADC with two potentiometers for speed and steer would also be much simpler. The rx and tx pins (PB6 and PB7)  however offer no adc (https://raw.githubusercontent.com/flo199213/Hoverboard-Firmware-Hack-Gen2/master/GD32F130C8%20Dokumentation/GD32F1x0_User_Manual.pdf page 16.)

But some led outputs could be configured as analog input (PA0 and PA1 for instance). You can find the accessible pins in inc/defines.h.

Have you succeeded to compile this firmware Gen2.0, flash it and the motors can be controlled via uart ?
If so, please send me detailed photos of your two control boards. I try to build a Gen2.x firmware and my pin assignemnts are totally different from what this firmware, yet the photo of the two circuit boards is identital to my board: https://github.com/RoboDurden/Hoverboard-Firmware-Hack-Gen2.x

RoboDurden, 2023-02-01:
You can now download compiled binaries for the V2.0 and V2.1 boards as well as tested Arduino examples on my fork: https://github.com/RoboDurden/Hoverboard-Firmware-Hack-Gen2.x

I can only test the PPM rc-receiver Arduino example with OVERWRITE_PPM as i do not have an rc-controller. Please share feedback.

Vorlovskis, 2023-06-04:
> You can now download compiled binaries for the V2.0 and V2.1 boards as well as tested Arduino examples on my fork: https://github.com/RoboDurden/Hoverboard-Firmware-Hack-Gen2.x
>
> I can only test the PPM rc-receiver Arduino example with OVERWRITE_PPM as i do not have an rc-controller. Please share feedback.

Hi. Can you share your experience with versions 2.0 dual mainboards?   stuck in visual studio error in LN34 no fail sourse found. Please help

RoboDurden, 2023-06-04:
i use the Keil ide for my gen2.x repo. PlatformIO uses a different tool chain so compiler errors might occour.
Right now we are trying to build a PlatformIO C++ SimpleFOC firmware for the GD32F130 Gen2 boards here: https://github.com/RoboDurden/Hoverboard-Firmware-Hack-Gen2.x/issues/11
As the GD32-Arduino-Core is still very buggy it is yet to be seen how easy that will be.
But if you have a Gen2.0 board or Gen1 Sideboard with GD32F130 you are very welcome to join the party.

Roland, from www.RoboDurden.de

Vorlovskis, 2023-06-04:
Thanks for reply. I am basicaly 0 in coding with basic in Arduino. If i can help with smth, just tell. My dual motherboards are GD32F130C8. One set 2.0, second is bit different after chip pinout to mosfets. But pins still same. Looking to use PWM Receiver.

RoboDurden, 2023-06-04:
for the 2.0 you can user my precompiled binaries. You will need an esp32 (hardware serial) or esp8266/arduino (software serial) anyway.

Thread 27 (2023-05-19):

done here: https://github.com/gaucho1978/CHEAP-LAWNMOWER-ROBOT-FROM-HOVERBOARD/blob/master/README.md

weiminshen99, 2023-05-19:
done here: https://github.com/gaucho1978/CHEAP-LAWNMOWER-ROBOT-FROM-HOVERBOARD/blob/master/README.md

_Originally posted by @gaucho1978 in https://github.com/flo199213/Hoverboard-Firmware-Hack-Gen2/issues/4#issuecomment-491603384_

weiminshen99, 2023-05-19:
Dear @gaucho1978,

I don't know if you are still active here, but thanks for your amazing repository for the LAWNMOWER-ROBOT!

When I compile your HoverboardPCBFirmware, I noticed that the <arm_math.h> is missing. Is it possible for you please to include it and other related .h files in the Inc/ directory of your repos?

Thanks!

Wingman

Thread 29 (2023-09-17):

Batt voltage when powered on ?

Fish-man134, 2023-09-17:
Hi I've have made a onewheel using these boards , I'd like to put a battery guage/meter in but only want it powered when the board is on.

Has anyone found anywhere that I can pull battery voltage only when the board is powered on?

I've probed into a few obvious places but can't find anything?

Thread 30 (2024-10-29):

Issues verifying the Arduino PMM

Smcgillis10, 2024-10-29:
Added the Arduino PPMDevice. and when verifying I am getting a ton of issues. Any help would be greatly appreciated.
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

Closed 2024-10-29.

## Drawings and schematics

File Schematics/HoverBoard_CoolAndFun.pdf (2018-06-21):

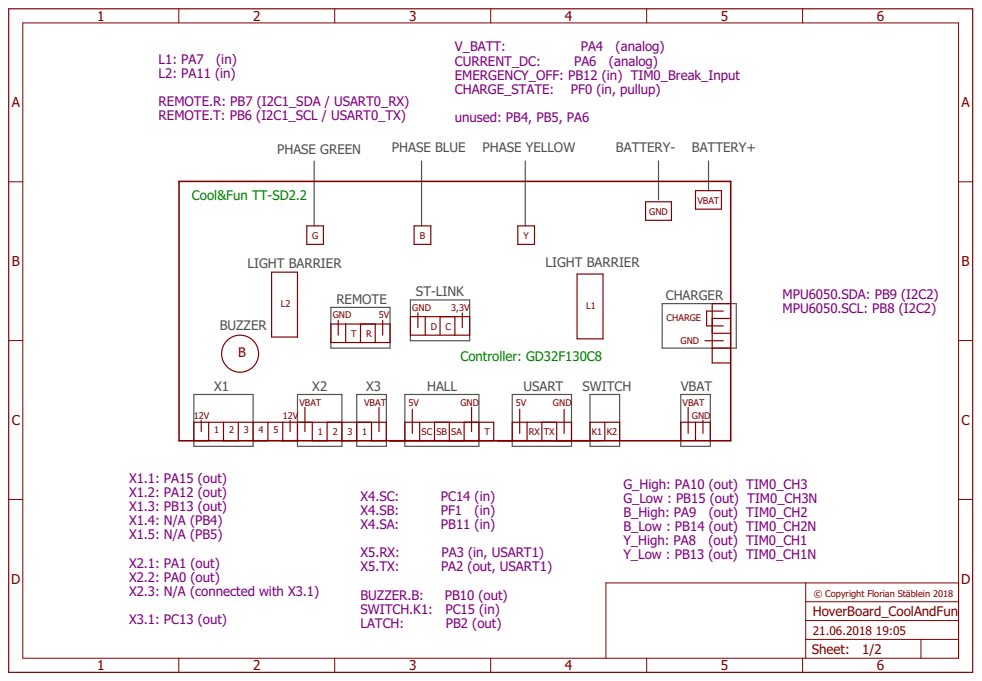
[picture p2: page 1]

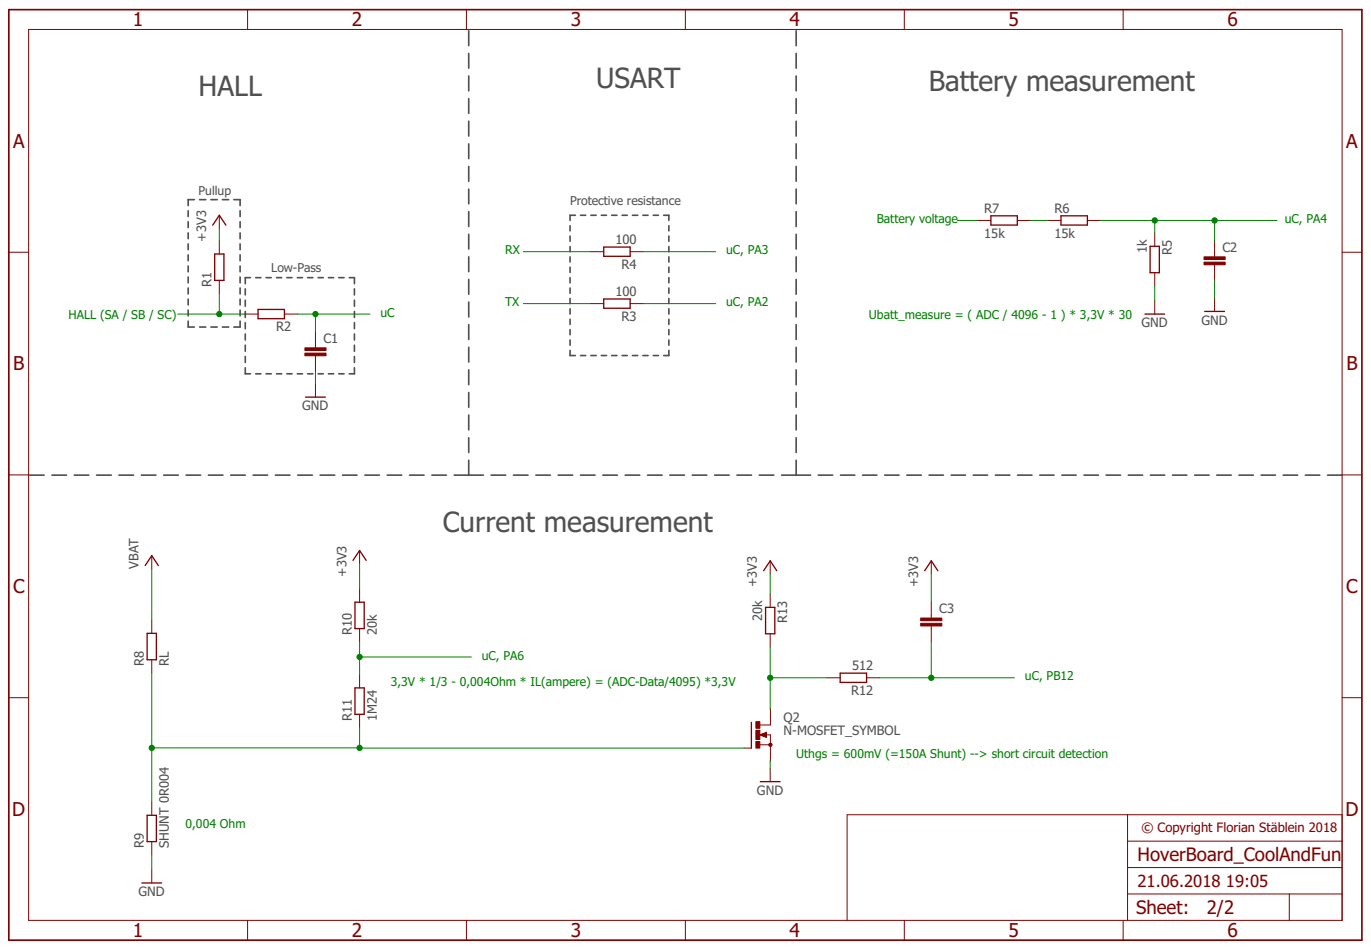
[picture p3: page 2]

Protective resistance | Battery measurement R7 R6

RL SHUNT 0R004 VBAT GND

3,3V * 1/3 - 0,004Ohm * IL(ampere) = (ADC-Data/4095) *3,3V

Uthgs = 600mV (=150A Shunt) --> short circuit detection

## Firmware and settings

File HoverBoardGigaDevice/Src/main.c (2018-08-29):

/*
* This file is part of the hoverboard-firmware-hack-V2 project. The 
* firmware is used to hack the generation 2 board of the hoverboard.
* These new hoverboards have no mainboard anymore. They consist of 
* two Sensorboards which have their own BLDC-Bridge per Motor and an
* ARM Cortex-M3 processor GD32F130C8.
*
* Copyright (C) 2018 Florian Staeblein
* Copyright (C) 2018 Jakob Broemauer
* Copyright (C) 2018 Kai Liebich
* Copyright (C) 2018 Christoph Lehnert
*
* The program is based on the hoverboard project by Niklas Fauth. The 
* structure was tried to be as similar as possible, so that everyone 
* could find a better way through the code.
*
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
* You should have received a copy of the GNU General Public License
* along with this program.  If not, see <http://www.gnu.org/licenses/>.
*/

#define ARM_MATH_CM3

#include "gd32f1x0.h"

#include "../Inc/setup.h"
#include "../Inc/defines.h"
#include "../Inc/config.h"
#include "../Inc/it.h"
#include "../Inc/bldc.h"
#include "../Inc/commsMasterSlave.h"
#include "../Inc/commsSteering.h"
#include "../Inc/commsBluetooth.h"
#include "stdio.h"
#include "stdlib.h"
#include "string.h"
#include <math.h>     
#include "arm_math.h" 

#ifdef MASTER
int32_t steer = 0; 												// global variable for steering. -1000 to 1000
int32_t speed = 0; 												// global variable for speed.    -1000 to 1000
FlagStatus activateWeakening = RESET;			// global variable for weakening
FlagStatus beepsBackwards = RESET;  			// global variable for beeps backwards
			
extern uint8_t buzzerFreq;    						// global variable for the buzzer pitch. can be 1, 2, 3, 4, 5, 6, 7...
extern uint8_t buzzerPattern; 						// global variable for the buzzer pattern. can be 1, 2, 3, 4, 5, 6, 7...
			
extern float batteryVoltage; 							// global variable for battery voltage
extern float currentDC; 									// global variable for current dc
extern float realSpeed; 									// global variable for real Speed
uint8_t slaveError = 0;										// global variable for slave error
	
extern FlagStatus timedOut;								// Timeoutvariable set by timeout timer

uint32_t inactivity_timeout_counter = 0;	// Inactivity counter
uint32_t steerCounter = 0;								// Steer counter for setting update rate

void ShowBatteryState(uint32_t pin);
void BeepsBackwards(FlagStatus beepsBackwards);
void ShutOff(void);
#endif

const float lookUpTableAngle[181] =  
{
  -1,
  -0.937202577,
  -0.878193767,
  -0.822607884,
  -0.770124422,
  -0.720461266,
  -0.673369096,
  -0.628626737,
  -0.58603728,
  -0.545424828,
  -0.506631749,
  -0.46951635,
  -0.433950895,
  -0.399819915,
  -0.367018754,
  -0.335452314,
  -0.30503398,
  -0.275684674,
  -0.24733204,
  -0.219909731,
  -0.193356783,
  -0.167617063,
  -0.142638788,
  -0.118374098,
  -0.094778672,
  -0.071811398,
  -0.049434068,
  -0.027611115,
  -0.006309372,
  0.014502141,
  0.03485241,
  0.054768601,
  0.074276213,
  0.093399224,
  0.112160212,
  0.130580478,
  0.148680146,
  0.166478264,
  0.183992885,
  0.201241154,
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
};


//----------------------------------------------------------------------------
// MAIN function
//----------------------------------------------------------------------------
int main (void)
{
#ifdef MASTER
	FlagStatus enable = RESET;
	FlagStatus enableSlave = RESET;
	FlagStatus chargeStateLowActive = SET;
	int16_t sendSlaveValue = 0;
	uint8_t sendSlaveIdentifier = 0;
	int8_t index = 8;
  int16_t pwmSlave = 0;
	int16_t pwmMaster = 0;
	int16_t scaledSpeed = 0;
	int16_t scaledSteer  = 0;
	float expo = 0;
	float steerAngle = 0;
	float xScale = 0;
#endif
	
	//SystemClock_Config();
  SystemCoreClockUpdate();
  SysTick_Config(SystemCoreClock / 100);
	
	// Init watchdog
	if (Watchdog_init() == ERROR)
	{
		// If an error accours with watchdog initialization do not start device
		while(1);
	}
	
	// Init Interrupts
	Interrupt_init();
	
	// Init timeout timer
	TimeoutTimer_init();
	
	// Init GPIOs
	GPIO_init();
	
	// Activate self hold direct after GPIO-init
	gpio_bit_write(SELF_HOLD_PORT, SELF_HOLD_PIN, SET);

	// Init usart master slave
	USART_MasterSlave_init();
	
	// Init ADC
	ADC_init();
	
	// Init PWM
	PWM_init();
	
	// Device has 1,6 seconds to do all the initialization
	// afterwards watchdog will be fired
	fwdgt_counter_reload();

	// Init usart steer/bluetooth
	USART_Steer_COM_init();

#ifdef MASTER
	// Startup-Sound
	for (; index >= 0; index--)
	{
    buzzerFreq = index;
    Delay(10);
  }
  buzzerFreq = 0;

	// Wait until button is pressed
	while (gpio_input_bit_get(BUTTON_PORT, BUTTON_PIN))
	{
		// Reload watchdog while button is pressed
		fwdgt_counter_reload();
	}
#endif

  while(1)
	{
#ifdef MASTER
		steerCounter++;	
		if ((steerCounter % 2) == 0)
		{	
			// Request steering data
			SendSteerDevice();
		}
		
		// Calculate expo rate for less steering with higher speeds
		expo = MAP((float)ABS(speed), 0, 1000, 1, 0.5);
		
	  // Each speedvalue or steervalue between 50 and -50 means absolutely no pwm
		// -> to get the device calm 'around zero speed'
		scaledSpeed = speed < 50 && speed > -50 ? 0 : CLAMP(speed, -1000, 1000) * SPEED_COEFFICIENT;
		scaledSteer = steer < 50 && steer > -50 ? 0 : CLAMP(steer, -1000, 1000) * STEER_COEFFICIENT * expo;
		
		// Map to an angle of 180 degress to 0 degrees for array access (means angle -90 to 90 degrees)
		steerAngle = MAP((float)scaledSteer, -1000, 1000, 180, 0);
		xScale = lookUpTableAngle[(uint16_t)steerAngle];

		// Mix steering and speed value for right and left speed
		if(steerAngle >= 90)
		{
			pwmSlave = CLAMP(scaledSpeed, -1000, 1000);
			pwmMaster = CLAMP(pwmSlave / xScale, -1000, 1000);
		}
		else
		{
			pwmMaster = CLAMP(scaledSpeed, -1000, 1000);
			pwmSlave = CLAMP(xScale * pwmMaster, -1000, 1000);
		}
		
		// Read charge state
		chargeStateLowActive = gpio_input_bit_get(CHARGE_STATE_PORT, CHARGE_STATE_PIN);
		
		// Enable is depending on charger is connected or not
		enable = chargeStateLowActive;
		
		// Enable channel output
		SetEnable(enable);

		// Decide if slave will be enabled
		enableSlave = (enable == SET && timedOut == RESET) ? SET : RESET;
		
		// Decide which process value has to be sent
		switch(sendSlaveIdentifier)
		{
			case 0:
				sendSlaveValue = currentDC * 100;
				break;
			case 1:
				sendSlaveValue = batteryVoltage * 100;
				break;
			case 2:
				sendSlaveValue = realSpeed * 100;
				break;
				default:
					break;
		}
		
    // Set output
		SetPWM(pwmMaster);
		SendSlave(-pwmSlave, enableSlave, RESET, chargeStateLowActive, sendSlaveIdentifier, sendSlaveValue);
		
		// Increment identifier
		sendSlaveIdentifier++;
		if (sendSlaveIdentifier > 2)
		{
			sendSlaveIdentifier = 0;
		}
		
		// Show green battery symbol when battery level BAT_LOW_LVL1 is reached
    if (batteryVoltage > BAT_LOW_LVL1)
		{
			// Show green battery light
			ShowBatteryState(LED_GREEN);
			
			// Beeps backwards
			BeepsBackwards(beepsBackwards);
		}
		// Make silent sound and show orange battery symbol when battery level BAT_LOW_LVL2 is reached
    else if (batteryVoltage > BAT_LOW_LVL2 && batteryVoltage < BAT_LOW_LVL1)
		{
			// Show orange battery light
			ShowBatteryState(LED_ORANGE);
			
      buzzerFreq = 5;
      buzzerPattern = 8;
    }
		// Make even more sound and show red battery symbol when battery level BAT_LOW_DEAD is reached
		else if  (batteryVoltage > BAT_LOW_DEAD && batteryVoltage < BAT_LOW_LVL2)
		{
			// Show red battery light
			ShowBatteryState(LED_RED);
			
      buzzerFreq = 5;
      buzzerPattern = 1;
    }
		// Shut device off, when battery is dead
		else if (batteryVoltage < BAT_LOW_DEAD)
		{
      ShutOff();
    }
		else
		{
			ShutOff();
    }

		// Shut device off when button is pressed
		if (gpio_input_bit_get(BUTTON_PORT, BUTTON_PIN))
		{
      while (gpio_input_bit_get(BUTTON_PORT, BUTTON_PIN)) {}
			ShutOff();
    }
		
		// Calculate inactivity timeout (Except, when charger is active -> keep device running)
    if (ABS(pwmMaster) > 50 || ABS(pwmSlave) > 50 || !chargeStateLowActive)
		{
      inactivity_timeout_counter = 0;
    }
		else
		{
      inactivity_timeout_counter++;
    }
		
		// Shut off device after INACTIVITY_TIMEOUT in minutes
    if (inactivity_timeout_counter > (INACTIVITY_TIMEOUT * 60 * 1000) / (DELAY_IN_MAIN_LOOP + 1))
		{ 
      ShutOff();
    }
#endif	

		Delay(DELAY_IN_MAIN_LOOP);
		
		// Reload watchdog (watchdog fires after 1,6 seconds)
		fwdgt_counter_reload();
  }
}

#ifdef MASTER
//----------------------------------------------------------------------------
// Turns the device off
//----------------------------------------------------------------------------
void ShutOff(void)
{
	int index = 0;

	buzzerPattern = 0;
	for (; index < 8; index++)
	{
		buzzerFreq = index;
		Delay(10);
	}
	buzzerFreq = 0;
	
	// Send shut off command to slave
	SendSlave(0, RESET, SET, RESET, RESET, RESET);
	
	// Disable usart
	usart_deinit(USART_MASTERSLAVE);
	
	// Set pwm and enable to off
	SetEnable(RESET);
	SetPWM(0);
	
	gpio_bit_write(SELF_HOLD_PORT, SELF_HOLD_PIN, RESET);
	while(1)
	{
		// Reload watchdog until device is off
		fwdgt_counter_reload();
	}
}

//----------------------------------------------------------------------------
// Shows the battery state on the LEDs
//----------------------------------------------------------------------------
void ShowBatteryState(uint32_t pin)
{
	gpio_bit_write(LED_GREEN_PORT, LED_GREEN, pin == LED_GREEN ? SET : RESET);
	gpio_bit_write(LED_ORANGE_PORT, LED_ORANGE, pin == LED_ORANGE ? SET : RESET);
	gpio_bit_write(LED_RED_PORT, LED_RED, pin == LED_RED ? SET : RESET);
}

//----------------------------------------------------------------------------
// Beeps while driving backwards
//----------------------------------------------------------------------------
void BeepsBackwards(FlagStatus beepsBackwards)
{
	// If the speed is less than -50, beep while driving backwards
	if (beepsBackwards == SET && speed < -50)
	{
		buzzerFreq = 5;
    buzzerPattern = 4;
	}
	else
	{
		buzzerFreq = 0;
		buzzerPattern = 0;
	}
}
#endif

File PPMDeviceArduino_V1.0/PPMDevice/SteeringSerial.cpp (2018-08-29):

/*
* This file is part of the hoverboard-firmware-hack-V2 project. The 
* firmware is used to hack the generation 2 board of the hoverboard.
* These new hoverboards have no mainboard anymore. They consist of 
* two Sensorboards which have their own BLDC-Bridge per Motor and an
* ARM Cortex-M3 processor GD32F130C8.
*
* Copyright (C) 2018 Florian Staeblein
* Copyright (C) 2018 Jakob Broemauer
* Copyright (C) 2018 Kai Liebich
* Copyright (C) 2018 Christoph Lehnert
*
* The program is based on the hoverboard project by Niklas Fauth. The 
* structure was tried to be as similar as possible, so that everyone 
* could find a better way through the code.
*
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
* You should have received a copy of the GNU General Public License
* along with this program.  If not, see <http://www.gnu.org/licenses/>.
*/

#include "SteeringSerial.h"

//----------------------------------------------------------------------------
// Variables
//----------------------------------------------------------------------------
int32_t speedValue = 0;
int32_t steerValue = 0;
uint8_t upperLEDMaster = 0;
uint8_t lowerLEDMaster = 0;
uint8_t mosfetOutMaster = 0;
uint8_t upperLEDSlave = 0;
uint8_t lowerLEDSlave = 0;
uint8_t mosfetOutSlave = 0;
uint8_t beepsBackwards = 0;
uint8_t activateWeakening = 0;

void SendBuffer(uint8_t buffer[], uint8_t length);
uint16_t CalcCRC(uint8_t *ptr, int count);

//----------------------------------------------------------------------------
// Initializes the steering serial
//----------------------------------------------------------------------------
void InitSteeringSerial(void)
{
  // Set up serial communication
  Serial.begin(19200, SERIAL_8N1);
}

//----------------------------------------------------------------------------
// Sets the speed value
//----------------------------------------------------------------------------
void SetSpeed(uint16_t data, float factor)
{
  int16_t tempValue = ((float)data * 2 ) - 3000.0;  // Value -1000 to 1000
  tempValue *= factor;
  tempValue = CLAMP(tempValue, -1000, 1000);        // Avoid calculation failure
  speedValue = tempValue;
}

//----------------------------------------------------------------------------
// Sets the steering value
//----------------------------------------------------------------------------
void SetSteer(uint16_t data)
{
  int16_t tempValue = ((float)data * 2 ) - 3000.0;  // Value -1000 to 1000
  tempValue = CLAMP(tempValue, -1000, 1000);        // Avoid calculation failure
  if (speedValue < 0)
  {
    steerValue *= -1;
  }
  steerValue = tempValue;
}

//----------------------------------------------------------------------------
// Sends answer to master device
//----------------------------------------------------------------------------
void SendAnswer(void)
{
  int index = 0;
  uint8_t buffer[9];
  uint8_t byte1 = 0;
  uint8_t byte2 = 0;
  uint8_t byte3 = 0;
  uint8_t byte4 = 0;
  
  uint8_t sendByte = 0;
  sendByte |= (activateWeakening << 7);
  sendByte |= (beepsBackwards << 6);
  sendByte |= (mosfetOutSlave << 5);
  sendByte |= (lowerLEDSlave << 4);
  sendByte |= (upperLEDSlave << 3);
  sendByte |= (mosfetOutMaster << 2);
  sendByte |= (lowerLEDMaster << 1);
  sendByte |= (upperLEDMaster << 0);
  
  uint16_t speedValue_Format = (uint16_t)(speedValue);
  byte1 |= (speedValue_Format >> 8) & 0xFF;
  byte2 |= speedValue_Format & 0xFF;

  uint16_t steerValue_Format = (uint16_t)(steerValue);
  byte3 |= (steerValue_Format >> 8) & 0xFF;
  byte4 |= steerValue_Format & 0xFF;
  
  // Send answer
  buffer[index++] = '/';
  buffer[index++] = byte1;
  buffer[index++] = byte2;
  buffer[index++] = byte3;
  buffer[index++] = byte4;
  buffer[index++] = sendByte;

  // Calculate CRC
  uint16_t crc = CalcCRC(buffer, index);
  buffer[index++] = (crc >> 8) & 0xFF;
  buffer[index++] = crc & 0xFF;

  // Stop byte
  buffer[index++] = '\n';
  
  SendBuffer(buffer, index);
}

//----------------------------------------------------------------------------
// Calculates CRC value
//----------------------------------------------------------------------------
uint16_t CalcCRC(uint8_t *ptr, int count)
{
  uint16_t  crc;
  uint8_t i;
  crc = 0;
  while (--count >= 0)
  {
    crc = crc ^ (uint16_t) *ptr++ << 8;
    i = 8;
    do
    {
      if (crc & 0x8000)
      {
        crc = crc << 1 ^ 0x1021;
      }
      else
      {
        crc = crc << 1;
      }
    } while(--i);
  }
  return (crc);
}

//----------------------------------------------------------------------------
// Sends buffer
//----------------------------------------------------------------------------
void SendBuffer(uint8_t buffer[], uint8_t length)
{
  uint8_t index = 0;
  
  for(; index < length; index++)
  {
    Serial.write(buffer[index]);
  }
}

//----------------------------------------------------------------------------
// Sends debug infos
//----------------------------------------------------------------------------
void SendDebug()
{
  Serial.print(speedValue);
  Serial.print(",");
  Serial.println(steerValue);
}

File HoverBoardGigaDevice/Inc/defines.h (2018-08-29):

/*
* This file is part of the hoverboard-firmware-hack-V2 project. The 
* firmware is used to hack the generation 2 board of the hoverboard.
* These new hoverboards have no mainboard anymore. They consist of 
* two Sensorboards which have their own BLDC-Bridge per Motor and an
* ARM Cortex-M3 processor GD32F130C8.
*
* Copyright (C) 2018 Florian Staeblein
* Copyright (C) 2018 Jakob Broemauer
* Copyright (C) 2018 Kai Liebich
* Copyright (C) 2018 Christoph Lehnert
*
* The program is based on the hoverboard project by Niklas Fauth. The 
* structure was tried to be as similar as possible, so that everyone 
* could find a better way through the code.
*
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
* You should have received a copy of the GNU General Public License
* along with this program.  If not, see <http://www.gnu.org/licenses/>.
*/

#ifndef DEFINES_H
#define DEFINES_H

#include "gd32f1x0.h"
#include "../Inc/config.h"

// LED defines
#define LED_GREEN GPIO_PIN_15
#define LED_GREEN_PORT GPIOA
#define LED_ORANGE GPIO_PIN_12
#define LED_ORANGE_PORT GPIOA
#define LED_RED GPIO_PIN_3
#define LED_RED_PORT GPIOB

#define UPPER_LED_PIN GPIO_PIN_1
#define UPPER_LED_PORT GPIOA
#define LOWER_LED_PIN GPIO_PIN_0
#define LOWER_LED_PORT GPIOA

// Mosfet output
#define MOSFET_OUT_PIN GPIO_PIN_13
#define MOSFET_OUT_PORT GPIOC

// Brushless Control DC (BLDC) defines
// Channel G
#define RCU_TIMER_BLDC RCU_TIMER0
#define TIMER_BLDC TIMER0
#define TIMER_BLDC_CHANNEL_G TIMER_CH_2
#define TIMER_BLDC_GH_PIN GPIO_PIN_10
#define TIMER_BLDC_GH_PORT GPIOA
#define TIMER_BLDC_GL_PIN GPIO_PIN_15
#define TIMER_BLDC_GL_PORT GPIOB
// Channel B
#define TIMER_BLDC_CHANNEL_B TIMER_CH_1
#define TIMER_BLDC_BH_PIN GPIO_PIN_9
#define TIMER_BLDC_BH_PORT GPIOA
#define TIMER_BLDC_BL_PIN GPIO_PIN_14
#define TIMER_BLDC_BL_PORT GPIOB
// Channel Y
#define TIMER_BLDC_CHANNEL_Y TIMER_CH_0
#define TIMER_BLDC_YH_PIN GPIO_PIN_8
#define TIMER_BLDC_YH_PORT GPIOA
#define TIMER_BLDC_YL_PIN GPIO_PIN_13
#define TIMER_BLDC_YL_PORT GPIOB

// Timer BLDC short circuit emergency shutoff define
#define TIMER_BLDC_EMERGENCY_SHUTDOWN_PIN GPIO_PIN_12
#define TIMER_BLDC_EMERGENCY_SHUTDOWN_PORT GPIOB

// Hall sensor defines
#define HALL_A_PIN GPIO_PIN_11
#define HALL_A_PORT GPIOB
#define HALL_B_PIN GPIO_PIN_1
#define HALL_B_PORT GPIOF
#define HALL_C_PIN GPIO_PIN_14
#define HALL_C_PORT GPIOC

// Usart master slave defines
#define USART_MASTERSLAVE USART1
#define USART_MASTERSLAVE_TX_PIN GPIO_PIN_2
#define USART_MASTERSLAVE_TX_PORT GPIOA
#define USART_MASTERSLAVE_RX_PIN GPIO_PIN_3
#define USART_MASTERSLAVE_RX_PORT GPIOA

// ADC defines
#define VBATT_PIN	GPIO_PIN_4
#define VBATT_PORT GPIOA
#define VBATT_CHANNEL ADC_CHANNEL_4
#define CURRENT_DC_PIN	GPIO_PIN_6
#define CURRENT_DC_PORT GPIOA
#define CURRENT_DC_CHANNEL ADC_CHANNEL_6

// Self hold defines
#define SELF_HOLD_PIN GPIO_PIN_2
#define SELF_HOLD_PORT GPIOB

// Button defines
#define BUTTON_PIN GPIO_PIN_15
#define BUTTON_PORT GPIOC

// Usart steer defines
#define USART_STEER_COM USART0
#define USART_STEER_COM_TX_PIN GPIO_PIN_6
#define USART_STEER_COM_TX_PORT GPIOB
#define USART_STEER_COM_RX_PIN GPIO_PIN_7
#define USART_STEER_COM_RX_PORT GPIOB

#ifdef MASTER
// Buzzer defins
#define BUZZER_PIN GPIO_PIN_10
#define BUZZER_PORT GPIOB

// Charge state defines
#define CHARGE_STATE_PIN GPIO_PIN_0
#define CHARGE_STATE_PORT GPIOF
#endif

// Debug pin defines
#define DEBUG_PIN GPIO_PIN_4
#define DEBUG_PORT GPIOB

// ADC value conversion defines
#define MOTOR_AMP_CONV_DC_AMP 0.201465201465  // 3,3V * 1/3 - 0,004Ohm * IL(ampere) = (ADC-Data/4095) *3,3V
#define ADC_BATTERY_VOLT      0.024169921875 	// V_Batt to V_BattMeasure = factor 30: ( (ADC-Data/4095) *3,3V *30 )

// Useful math function defines
#define ABS(a) (((a) < 0.0) ? -(a) : (a))
#define CLAMP(x, low, high) (((x) > (high)) ? (high) : (((x) < (low)) ? (low) : (x)))
#define MAX(x, high) (((x) > (high)) ? (high) : (x))
#define MAP(x, xMin, xMax, yMin, yMax) ((x - xMin) * (yMax - yMin) / (xMax - xMin) + yMin)

// ADC buffer struct
typedef struct
{
  uint16_t v_batt;
	uint16_t current_dc;
} adc_buf_t;

#endif

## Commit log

2018-06-21 Schematics added
    [HoverBoard_CoolAndFun.sch]
2018-06-21 Added Schematics to readme
2018-08-29 Documentation of ARM Processor added
2018-08-29 Arduino Device Added for sending steering Data
    Arduino decodes RC receiver and sends steering data via USART
2018-08-29 Documentation for communication protocol added
    [CommunicationOverview.ods]
2018-08-29 Special documentation for the lipo battery

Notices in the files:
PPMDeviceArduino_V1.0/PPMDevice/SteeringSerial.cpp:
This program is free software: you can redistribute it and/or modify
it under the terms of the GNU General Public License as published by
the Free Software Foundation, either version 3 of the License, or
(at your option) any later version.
